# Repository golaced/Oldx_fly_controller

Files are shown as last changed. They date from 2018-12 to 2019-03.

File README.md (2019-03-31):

# 1 OLDX-开源多旋翼开发平台项目  
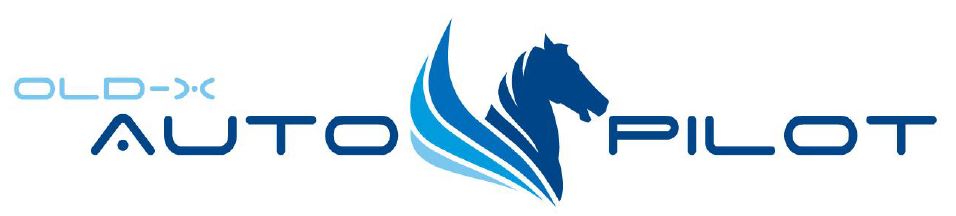
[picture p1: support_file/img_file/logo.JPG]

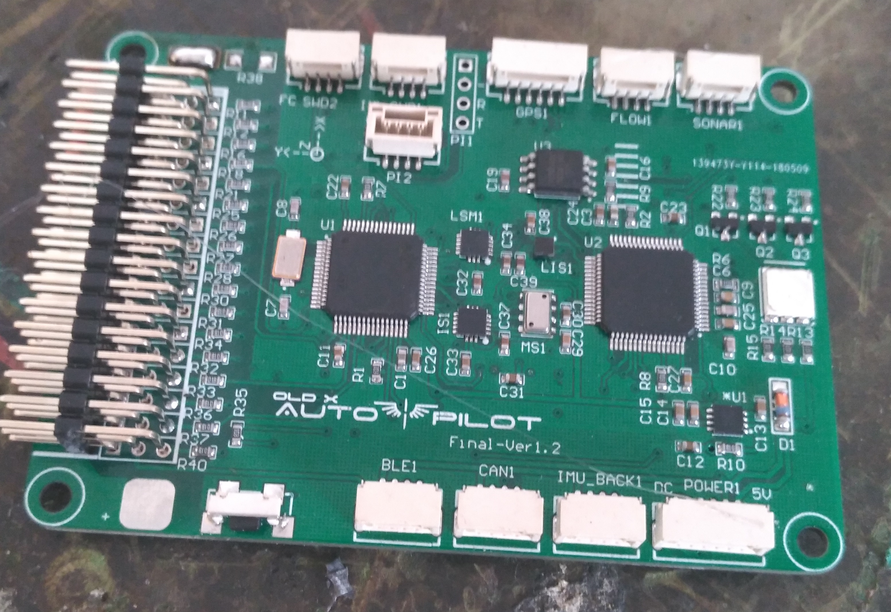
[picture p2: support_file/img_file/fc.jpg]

____OLDX多旋翼开发平台（OLDX-FC）是由北京理工大学自动化学院所属《北理云逸科技》团队开发的一个目前国内最完整的免费开源飞控项目，随着国内开源飞控的逐步发展如匿名、
INF、无名和ACFly飞控的陆续推出，如光流、气压计和GPS等相关算法已经逐步完善，但是相比Pixhawk等国外开源飞控平台的发展和定位仍然有发展空间。OLDX-FC于14年开始对多旋翼飞行器进行研究期间也经历过开源和借鉴的过程，为希望进一步推动国内开源飞控协作开发和
相互学习、相互分享的趋势，团队将该OLDX-FC转化为开源项目，采用自由捐赠的形式继续发展。<br>
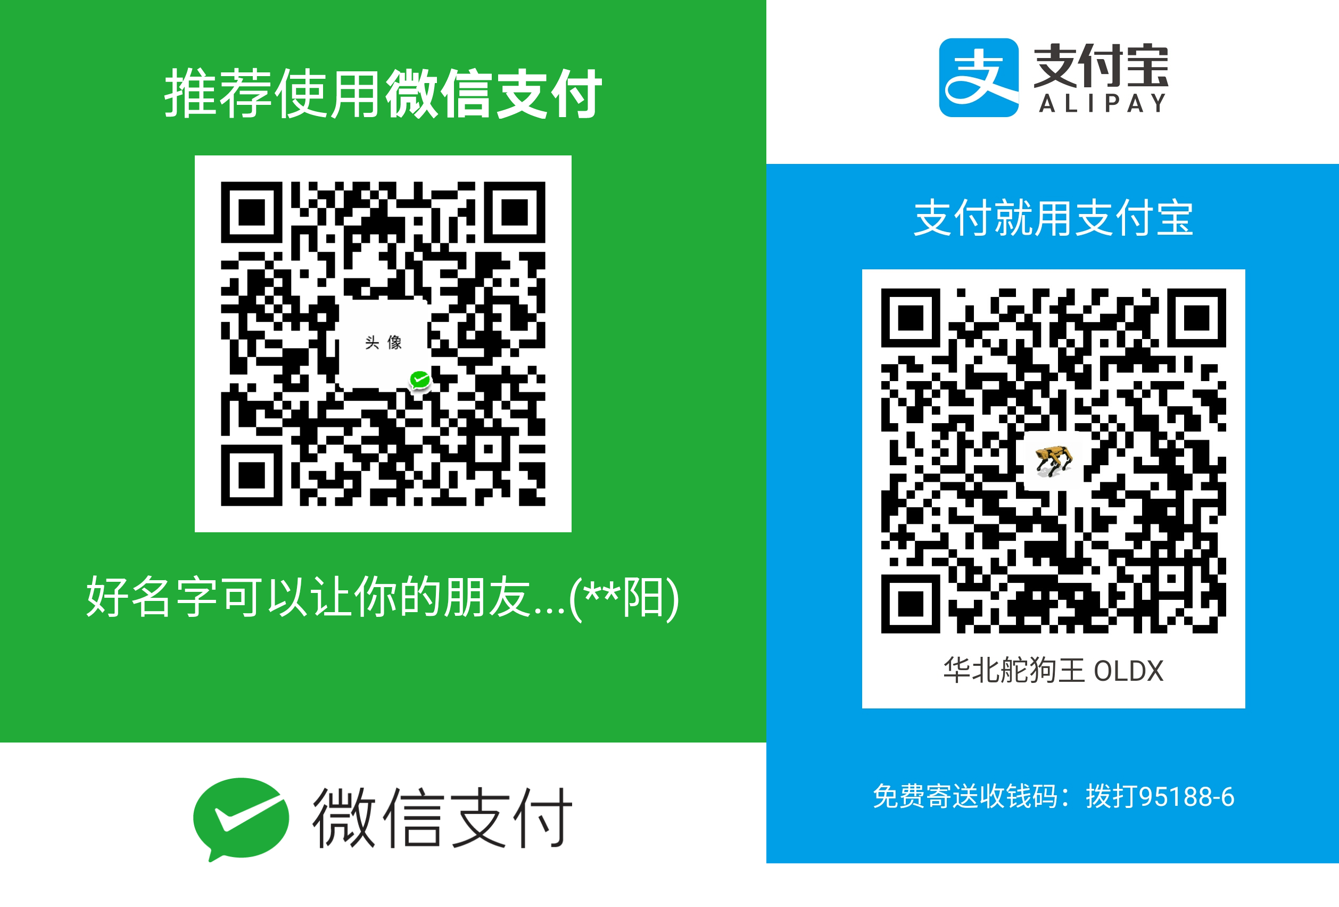
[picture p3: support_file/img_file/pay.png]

项目遵循GPL协议，能自由下载项目PCB进行加工使用但请勿作为商业用途，开源所有飞行控制和组合导航源码，可以进行修改和二次开发。<br><br><br>

**项目荣誉**

项目|奖项|年份
-------------|-------------|-------------
IMAV国际微小型无人机大赛|室外赛第3名  室内最佳自动化|2018
中航工业杯|三等奖|2018
IMAV国际微小型无人机大赛|室外赛第5名|2017
中航工业杯|二等奖|2017
中航工业杯|三等奖|2016

**-如果该项目对您有帮助请 Star 我们的项目-**<br>
**-如果您愿意分享对该项目的优化和改进请联系golaced@163.com或加入我们的QQ群567423074，加速开源项目的进度-**<br>

# 2 基本功能介绍
____OLDX-FC是一个基于STM32F4系列单片机的多旋翼飞控平台，其采用双处理器、双IMU冗余的设计，飞行控制和组合导航分别运行与不同的单片机中基于串口DMA进行高速数据交互
板载两套6轴惯性传感器、1个三轴磁力计、1个气压计并支持外部罗盘接入。组合导航CPU采用UCosII嵌入式操作系统基于卡尔曼滤波算法实现对GPS、光流、UWB和气压计数据的可靠
融合，从而实现室内外可靠的悬停和航线飞行，姿态和高度控制采用自抗扰（ADRC）控制算法实现对外部扰动的可靠控制同时具有响应快、信号跟踪性能好的特点，通过对自抗扰算法
改进实现了基于飞行器轴距、姿态、航向和高度三通道感度和快速调参。飞控在内部封装SDK二次开发接口和部分Demo，能快速实现一键起飞降落，视觉降落，目标跟踪和自主避障，
另外预留多个扩接口能作为地面机器人、无人车和无人船的硬件载体。飞控源码移植了Mavlink航向设置源码能实现基于Qground和MissonPlanner的任意航点、高度和速度的设置，
基于匿名地面站能实现对飞控内部任意融合结果、传感器参数、控制反馈期望和状态信息的实时显示和参数调节，基于板载NRF2.4通讯芯片能与地面手持遥控实现最远900米
的数据交互，实时显示飞行器经纬度、姿态，并对任意参数进行在线设定和修改，免去室外参数调节需要携带电脑和平板的不便。<br>



**飞控特性**：<br>
	*UCosII操作系统(正点原子)<br>
	*自抗扰姿态控制<br>
	*卡尔曼组合导航<br>
	*SDK快速开发<br>
	*Mavlink航线规划和匿名地面站快速调参<br>
	*移动遥控端状态显示和参数在线修改<br>
	*GPS导航、视觉导航、自动降落、光流图像定位<br>

**飞控性能演示视频连接：**<br>
	[SDK开发演示](https://v.youku.com/v_show/id_XMzc4MzAyMDU4MA==.html?spm=a2hzp.8244740.0.0&f=49551028) <br>
	[室外GPS航线测绘和地面站航点设置](https://i.youku.com/i/UMTU1NTgzMzYw?spm=a2hzp.8253869.0.0) <br>
	[视觉固定目标降落](https://v.youku.com/v_show/id_XMzk2OTMyNzE4MA==.html?spm=a2hzp.8253869.0.0) <br>
	[视觉移动小车降落](https://v.youku.com/v_show/id_XMzc0MTI4NzQ2NA==.html?spm=a2hzp.8253869.0.0) <br>
	[室内二维码地标阵列定位](https://v.youku.com/v_show/id_XMjc2MDAxMDI1Mg==.html?spm=a2hzp.8253869.0.0) <br>
	[室外光流悬停](https://v.youku.com/v_show/id_XMjc1NzI1NDQ4NA==.html?spm=a2hzp.8253869.0.0) <br>
	[室内气压计定高](https://v.youku.com/v_show/id_XMjcyNjM2MzU5Mg==.html?spm=a2hzp.8253869.0.0) <br>

# 3 PCB硬件参数
____OLDX-FC硬件采用4层板设计，通过外部电源模块进行供电支持2S~4S电池供电，具有最大12路PWM输出4路AD信号输入，板载NRF2.4通讯芯片，预留6路串口1路CAN接口<br>
  
**硬件参数：**

项目|参数
-------------|-------------
处理器|STM32F405RGT6-2
处理器性能|32Bit ARM Cortex-M4 168MH
陀螺仪 加速度计|ICM20602 + LSM6DS33
磁力计|LIS3MDL
气压计|MS5611
预留接口|GPS-1 串口-4 CAN-1 图像-1
PWM 输出通道|8 通道PWM + 4 路AUX
供电|5V输入 IO输出5V
飞行器类型|四旋翼 六旋翼 八旋翼 共轴六旋翼
高度悬停精度|±0.02m（超声波） ±0.1m（气压计）
位置悬停精度|±0.2m（GPS） ±0.1m（光流）

<br><br>
**飞控外壳：**<br>
____提供飞控3D打印外壳STL文件，设计为气压计增加缓冲空间并设计了减震球底座。
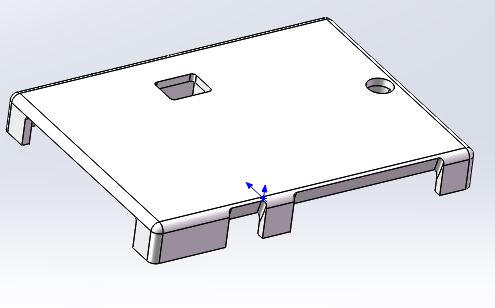
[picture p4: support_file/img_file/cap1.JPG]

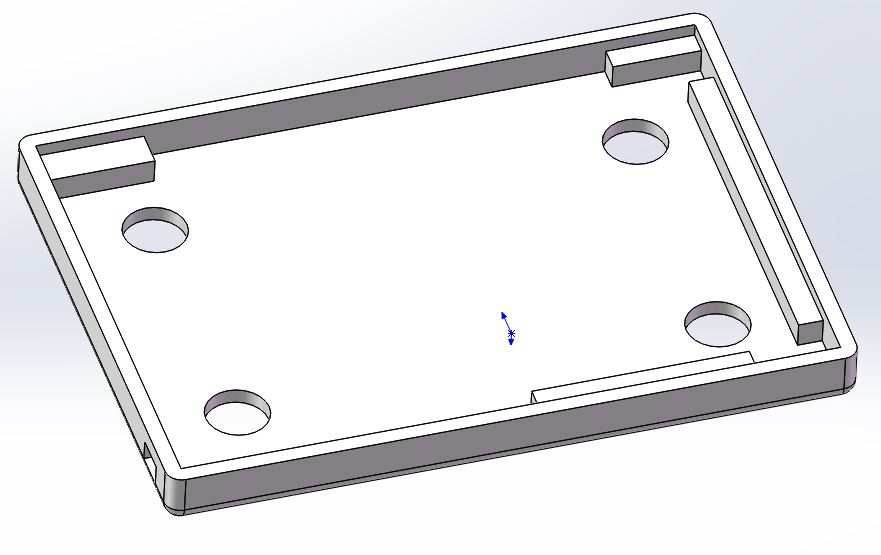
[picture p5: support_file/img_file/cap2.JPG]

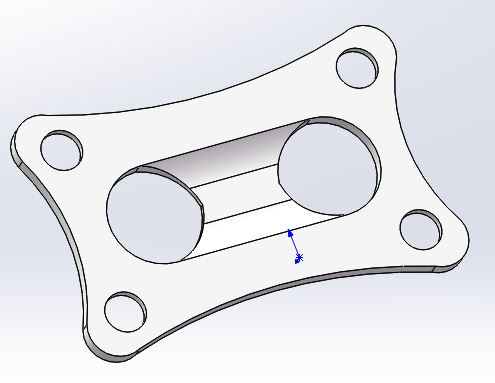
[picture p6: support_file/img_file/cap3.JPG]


# 4 软件说明
____OLDX-FC基于C语言和Keil5进行开发，飞行控制部分基于匿名早期裸奔程序架构，采用状态机调度保证不同线程的运行周期，
对其姿态控制部分进行修改，采用SO3下的旋转矩阵求取外环控制误差，姿态内环采用改进ADRC控制器保证对给的角速度的
稳定跟踪；高度控制部分替换原始互补滤波融合算法采用扩展卡尔曼滤波器融合气压计和加速度计，同样使用ADRC控制器控制
高速速度环。位置方面通过串口数据接收组合导航模块解算机体速度和位置，采用位置+速度+加速度三环控制飞行器位置；
通讯方面在保留匿名上位机调参功能外增加2.4G无线通讯，可脱离遥控器采用体感进行飞行器控制，另外移植Mavlink通讯协议实现
与Qground和MissonPlanner地面站的通信，实现室外飞行器航点设置和轨迹显示；增加SDK二次开发接口，封装了多种常用函数，如
速度给定，位置移动给定，航向飞行，图像目标对准，图像目标跟踪，地标引导降落的多个子API，通过简单的流程书写既可以实现
复杂的智能导航、图像导航功能，十分适合于Demo研发、电子竞赛、无人机竞赛和DIY开发中。<br>
____组合导航模块基于UCOSII操作系统，基于UKF和KF算法完成GPS、UWB、光流与加速度传感器数据的融合，采用非线性AHRS算法实现
可靠的姿态解算和机体加速度解算，同时预留CAN总线接口方便后续外扩其他传感器数据。

<br><br>
**飞行控制模块**

项目|参数
-------------|-------------
姿态解算|互补滤波(匿名)
高度融合|扩展卡尔曼(PX4)/抗差卡尔曼
姿态控制|SO(3)误差(PX4)+PD(角度)+ADRC(角速度)
高度控制|PD(高度)+ADRC(垂直速度)
位置控制|PD(高度)+PID(机体速度)+P(机体加速度)
通讯接口|2.4G无线通讯(匿名+OLDX手持遥控器) 串口数传(匿名+Mavlink)
控制方式|遥控器(PPM+SBUS) OLDX手持遥控器 SDK自主飞行
外部控制信号|4路舵机输出  支持使用飞控姿态控制两轴舵机云台稳相和无刷云台目标跟踪(RobotMaster)
地面站支持|匿名地面站(参数显示+波形显示+参数设置)  Qground/MissionPlanner(位姿轨迹显示+航点写入)

<br><br>
**组合导航模块**

项目|参数
-------------|-------------
姿态解算|非线性AHRS/梯度下降/扩展卡尔曼/互补滤波(匿名)
位置融合|抗差卡尔曼/无迹卡尔曼(AutoQuad)
传感器接口|GPS(NEO-8M 乐迪迷你)+UWB(INF)+光流(Pixflow/OLDX-AMF)+超声波(串口/PWM)+激光测距仪(VL53L0X)

# 5 飞控使用教程
## 5.1 PCB接口说明

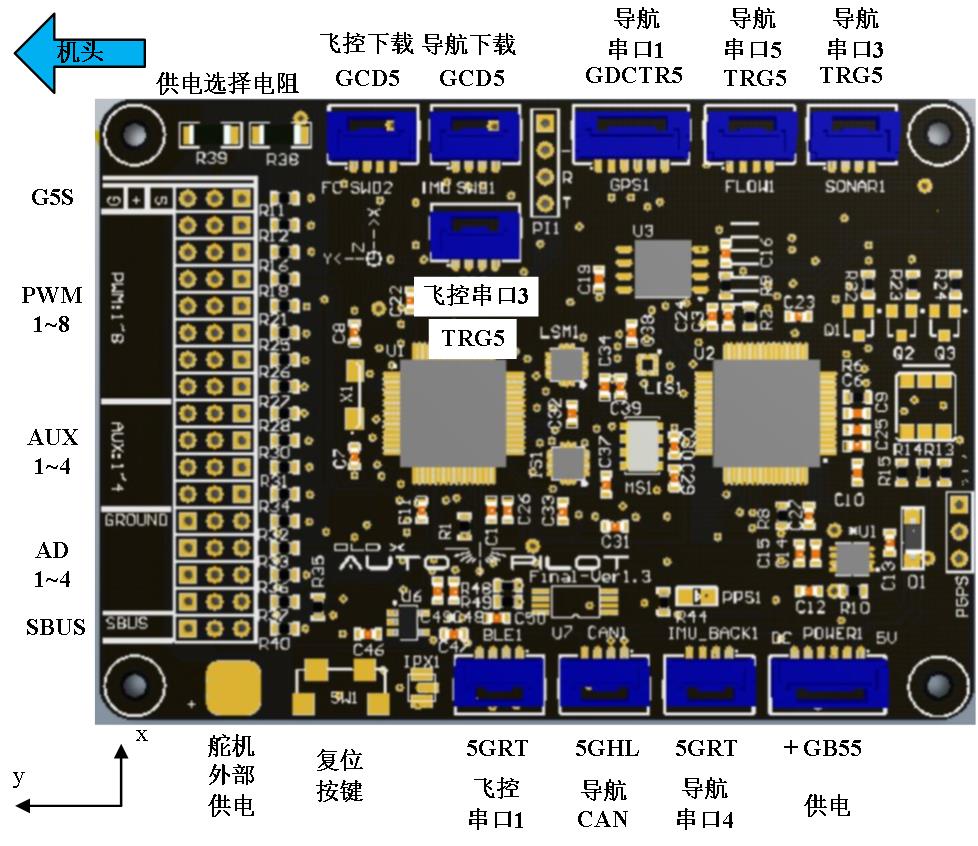
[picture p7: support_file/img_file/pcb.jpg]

<br><br>

接口|说明|支持模块
-------------|-------------|-------------
飞控下载|飞控模块SWD下载口|download_fc模块 C->SCLK D->SWD
导航下载|导航模块SWD下载口|download_stlink模块
导航串口1|GPS和外部罗盘IIC接口|乐迪M8N Mini GPS C->SCL D->SDA
导航串口5|光流传感器接口|Pixflow  OLDX-AMF
导航串口3|超声波接口|US100 (串口模式下T->T R->R)  北醒激光测距模块
导航串口4|预留传感器接口|
导航CAN|预留CAN总线接口|
飞控串口3|图像处理接口|树莓派  Odroid-XU4 （图像处理器需自行供电）
飞控串口1|数传接口|匿名数传 3DR数传  CUAV WIFI数传
PWM1~8|电调接口|400Hz
AUX1~4|电调9~12/舵机控制接口 1俯仰 2横滚 3投递器开关|两轴舵机云台 两轴无刷云台
AD1~4|模拟电压采集接口|压力传感器AD(0~3.3V)
SBUS|接收机接口|天地飞接收机 Futaba接收机
舵机供电选择|R39外部供电 R38飞控供电 （任选一）|
供电|采用6P自锁双头端子线与供电模块连续|power模块 +->DC B->蜂鸣器信号 5->5V降压输入

<br><br>
**OLDX飞控最少所需配置**

模块组合|实现功能
-------------|-------------
飞控+Power模块|手动飞行/气压定高
飞控+Power模块+光流|手动飞行/气压定高/超声定高/光流悬停/SDK飞行
飞控+Power模块+GPS|手动飞行/气压定高/GPS航线飞行/SDK飞行
飞控+Power模块+GPS/光流+树莓派/Odroid|手动飞行/气压定高/GPS航线飞行/SDK飞行/图像导航/视觉降落

<br><br>
**接线示意图**
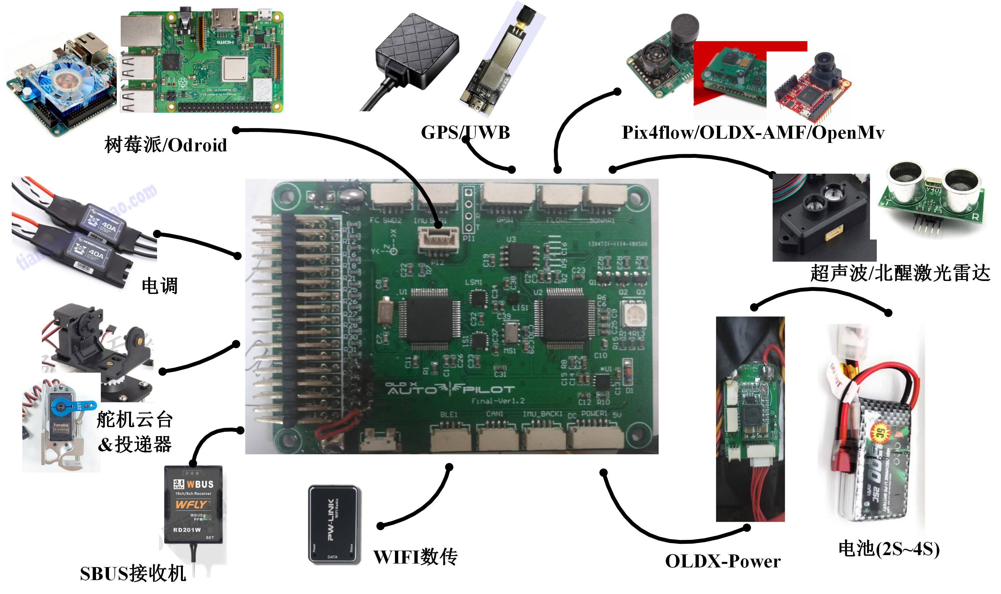
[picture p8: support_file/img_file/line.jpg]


## 5.2 程序宏定义和飞控配置说明
### 5.2.1 遥控器通道

通道|功能|通道说明
-------------|-------------|-------------
CH1|横滚通道|
CH2|俯仰通道|
CH3|油门通道|
CH4|航向通道|
CH5|SDK模式使能|  通道值<1500(关闭自动SDK飞行) 通道值>1500(使能自动SDK飞行)
CH6|返航和自动起飞| 通道值<1500(打开AUX3口开关) 通道值>1500(关闭AUX3口开关)
CH7|位置模式|  通道值<1500(手动) 通道值=1500(速度悬停) 通道值>1500(位置悬停)
CH8|高度模式|  通道值<1500(超声波 气压计自动切换) 通道值=1500(气压计) 通道值>1500(手动)

**飞行器解锁上锁**：外八遥控操作<br>
**飞行中关闭遥控器**：自动返航/自动降落/电机急停<br>
**自动起飞和智能飞行**：CH5>1500 CH6>1500 CH7>1500 CH8<1500  状态下外八解锁  并把油门置于中位(自主飞行中任意遥感不在中位均会进入自主飞行模式，
回复中位后继续执行当前任务。需要取消飞行则保证CH5<1500) <br>
**自主任务状态机重置**：在飞行器执行自主任务后无论自动降落或者人工打断都需在着陆上锁后保证CH5<1500 CH7<1500<br>
**飞行中自动返航**：无论在自主飞行或人工遥控飞行中 如果CH6通道值从大于1500切换到小于1500则进入失控策略，过程中可以通过人为遥控打断，并重新进行触发<br>
**陀螺仪校准**：CH8<1500 时CH7从小于1500到大于1500 快速切换多次<br>
**磁力计校准**：CH8>1500 时CH7从小于1500到大于1500 快速切换多次，进入模式后BB响持续发声，蓝色1s间隔闪烁<br>

## 5.3 飞行器配置和控制参数调整说明
### 5.3.1 飞行器配置
（1）飞控模块include.h<br>

宏定义|说明
-------------|-------------
USE_OLDX_REMOTE|使用OLDX手持遥控器代替传统遥控器
AUTO_MISSION|使能SDK飞行 
MAXMOTORS|最大电机数量（4/6/8/12）
FLASH_USE_STM32|使用STM32内部EPRoom模拟Flash  使能则无法存储GPS航点
YAW_INVER|航向控制输出方向 用于电机转向与标准方向不对下的软件调整，不用重新安装电机
YAW_FC|不使用磁力计修正航向
MAX_CTRL_ANGLE|最大控制姿态角度
MAX_CTRL_YAW_SPEED_RC|最大控制航向角速度
ESO_AI|姿态控制内环ADRC b0参数（0表示不使用ADRC控制器）
ESO_YI|航向控制内环ADRC b0参数（0表示不使用ADRC控制器）
HOLD_THR_PWM|预设悬停油门
DEBUG_MODE|室内则封闭PWM输出，解锁后电机不转动可以作为室内Debug使用
TUNING_ONE_AXIX|使能则参数调节时仅针对一个轴
TUNING_X/ TUNING_Z|单轴调参目标
USE_KF|使用带估计加速度偏差的卡尔曼滤波器估计高度否则使用PX4提供的EKF高度估计算法
USE_CARGO|使用AUX3的舵机投递器

（2）飞控模块oldx_api.h<br>

宏定义|说明
-------------|-------------
LAND_SPD|自动降落速度
MAX_WAYP_Z|最大航点高度限制
WAY_POINT_DEAD1|航点达到判断死区
LAND_CHECK_G|着地检测重量加速度
LAND_CHECK_TIME|着地检测条件判断时间
YAW_LIMIT_RATE|旋转航向最大角速度限制 

（3）导航模块include.h<br>

宏定义|说明
-------------|-------------
USE_UKF_FROM_AUTOQUAD|使用Autoquad提供的UKF融合算法(存在Bug)
UKF_IN_ONE_THREAD|UKF融合时不使用UcosII系统
USE_US100/ USE_KS103/ USE_LIDAR|定高传感器数据选择
SONAR_SAMPLE1/ SONAR_SAMPLE2/ SONAR_SAMPLE3|高度传感器数据采样频率
USE_IMU_BACK_IO_AS_SONAR|使用串口4采集高度传感器数据
SONAR_USE_FLOW|直接使用Pixflow传感器自带超声波高度数据

<br><br>
**飞行器型号设置**：<br>
（1）采用如下宏定义定义你的飞行器<br>

```
#if defined(M_DRONE)
#define M_DRONE_ID     //单片机id_chip值
#define PX4_SDK 0  
//#define PX4_LINK
#define USE_MINI_FC_FLOW_BOARD 0 
#define USE_VER_8_PWM 1  
#define USE_VER_8 0  
#define USE_VER_7 1
#define USE_OLDX_REMOTE 0

#define BLDC_PAN
#define W2C_MARK
#define USE_CIRCLE 0
//#define USE_LED 
//#define USE_CARGO     //可修改
#define AUTO_MISSION    //可修改

//#define USE_KF	    //可修改 
#define USE_UWB
#define MAXMOTORS 		(4)		//可修改
#define FLASH_USE_STM32 0       //可修改
#define YAW_INVER 	  0		    //可修改
#define YAW_FC 0  				//可修改
#define MAX_CTRL_ANGLE			30.0f	//可修改
#define MAX_CTRL_YAW_SPEED_RC   200	    //可修改

#define ESO_AI 22  //可修改
#define ESO_YI 22  //可修改
//
#define TRAJ1_1  2//2 circle 1 line  3 way points   4 jerk  5 car
#define HOLD_THR_PWM  LIMIT(500,0,500)  //可修改
#endif
```
<br>
并在24~42行"唯一"定义该机型：
<br>

```
#define M_DRONE
//#define M_DRONE250X4
//#define M_DRONE_330X6
//#define M_DRONE_330 
//#define M_DRONE_PX4
//#define M_CAR
```

<br>
并在init.c 43行定义飞控对应2.4G通讯通道CHE，修改188行 mode_oldx.rc_loss_return_home选择失控模式(0上锁 1返航 2降落 3无视)
<br>

```
switch(id_chip)
{
case M_DRONE_ID: CHE=25;break;
case IMAV2: CHE=22;break;
case IMAV3: CHE=33;break;
default: CHE=11;break;
}
```

<br>
并在pos_ctrl.c 854行定义使用的SDK：
<br>

```
switch(mission_sel_lock)
{
case 0:
switch(id_chip)
{
case M_DRONE_ID: mission_flag=mission_test_gps(T); break;//你的SDK
case IMAV2: mission_flag=mission_search(T); break;
case IMAV3: mission_flag=mission_test_gps(T); break;
default:mission_flag=mission_test_gps(T); break;
}	
break;
```

<br>
并在scheduer.c 152行定义UART_UP_LOAD_SEL选择上位机波形显示队列
<br>

### 5.3.2 参数调节
____飞控已经集成基础参数调节功能在完成飞行器机型设置和固件更新后，进行传感器校准即刻起飞或者进行参数调节。<br>
(1)远程调参与波形显示<br>
____飞控默认采用2.4G无线与OLDX手持遥控端进行通讯，参数调节可以直接通过遥控器实现，另外手持遥控器同时具有USB虚拟串口，
遥控器工作后连接PC机则可以使用匿名地面站进行参数调节(115200默认波特率)和参数波形显示。(注：对手持控制器来说需要在PID参数界面
等等数据全部接受完成后在进行调参，否则会出现参数误写入引起的炸鸡；对地面站同样也是建议在数据通信正常后最少读取5次PID参数避免误写入问题)
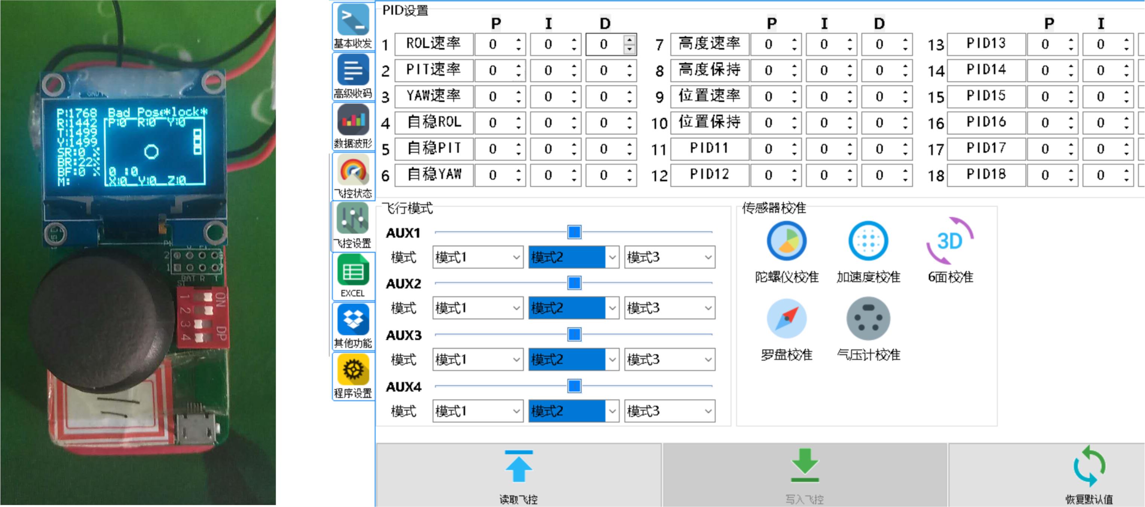
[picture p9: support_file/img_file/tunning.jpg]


(2)姿态参数调节<br>
____飞控安装好后首先需要进行姿态参数的调节推荐采用万向轴或烤四轴的方式固定飞行器进行参数调节，通过选择调参模式确认是单轴还是全向调参：

```
TUNING_ONE_AXIX 0
TUNING_X 0
TUNING_Z 0
```

默认都为0则飞行器全向参数都可调节，则以该情况为例设置 UART_UP_LOAD_SEL=11 使能上位机波形显示为姿态参数调节序列，通过CH6(>1500外环)能选择显示内环还是
外环的期望和给的参数，则波形中Ax Ay Az为期望的横滚 俯仰 航向值，Gx Gy Gz为对应反馈值，Hx Hy Hz为对应误差。参数调节时如果外环PID参数有值则
遥杆给定期望角度，如无值则给定期望角速度。<br>

A.如飞行器机架小于550轴距可直接调整感度来快速完成参数调节，使用手动模式起飞保证飞行器离地观测姿态控制是否响应迅速，
是否存在超调和抖动，感度对应PID参数为：<br>

参数|说明|默认值
-------------|-------------|-------------
PID17-P|横滚、俯仰感度(增大则等于增大飞机调节增益)|1000
PID17-I|航向感度|1000
PID17-D|高度感度|1000

<br><br>

飞行器机型|主要动力配置|飞行器感度
-------------|-------------|-------------
330X4四轴|3s 4000mah  1500kv*4 好赢乐天15A 8寸桨|俯仰:1000    航向:1000   高度:1000   b0:22
450X4四轴|4s 4000mah  920kv*4 好赢乐天20A 9寸桨|俯仰:820    航向:1000   高度:1100   b0:22
6轴泡沫机|3s 10000mah  920kv*6  Emax 40A  8寸桨|俯仰:300    航向:200   高度:100  b0:3.5
共轴反桨6轴涵道|6s 10000mah 450kv*12 Emax40A 9寸桨|俯仰:250   航向:280   高度:68   b0:2.2
6轴飞行器+小车底盘|6s 16000mah *2 180kv *6 Emax40A 14寸桨|俯仰:325 航向:168 高度:100 b0:0 II:400 ID:4500 OP:368 P_GAIN:100

B.如飞行器轴距较大，电机KV值较小则不推荐采用起飞调参的方式，在调试架上固定好飞行器后采用手动模式解锁调参并内外环波形曲线。
调参时首先将ADRC控制器b0置0不使用其控制输出，将外环PID清0仅调整角速度环，解锁后观察飞行器是否能较好地跟踪遥控给定速度，
在能保证基本跟踪上后将姿态ADRC b0在22-300进行调整(默认220)，如果飞机出现晃动则减小，出现顿挫则增大，在基本实现跟踪期望速度后(可存在一定
滞后，特别是大飞机)通过拉拽飞行器轴造成外部扰动和控制器饱和来确定是否需要增大D，如果出现按压时的超调可增大D来保证回弹的柔和。<br>
在完成内环参数调节后，设置外环P参数(默500-700)，在保证出现一定超调下的P时增加D达到最终回中无快速无超调(550以下小飞机可能不需要D)，之后
同样采用人为拉拽或按压测试控制器饱和回中是否出现超调和震荡判断参数是否合适。<br>
对航向来说一般仅需要调整感度既可以满足一般应用，如有更高性能要求可采用类似如上的方式进行参数调节，另外航向ADRC b0参数推荐仅在小轴距飞行器
上使用，则姿态调节对应PID参数表如下：<br>

参数|说明|默认值
-------------|-------------|-------------
PID1-P|横滚、俯仰 内环P|700
PID1-I|横滚、俯仰 内环I|200
PID1-D|横滚、俯仰 内环D|2200
PID2-P|姿态ADRC  b0|220
PID2-I|航向ADRC  b0|220
PID2-D|ADRC 控制死区|268
PID3-P|航向 内环P|1200
PID3-I|航向 内环I|100
PID3-D|航向 内环D|1200
PID4-P|横滚、俯仰 外环P|700
PID4-I|横滚、俯仰 外环I|0
PID4-D|横滚、俯仰 外环D|0
PID6-P|航向 外环P|800
PID6-I|航向 外环I|50
PID6-D|航向 外环D|300

在完成参数调节后可以采用两种方式将其保存在Flash中，对于感度可以采用遥控触发陀螺仪的方式写入(水平静置)，但还是推荐采用在代码里修改的方式。
其中对于ADRC b0参数在机型宏定义中修改，飞行器感度在Debug watch中修改后选择校准陀螺仪(见6.4.2小节)保存，姿态PID则在parameter.c 40行中进行修改:

```
float pid_att_out[3]={0.7,0.0,0.0};
float pid_att_in[3]={0.7,0.2,2.2};

float pid_att_out_yaw[3]={0.8,0.05,0.3};
float pid_att_in_yaw[3]={1.2,0.1,1.2};
```

(3)高度参数调节<br>
____高度参数调节方式类似姿态调节，如对性能要求不高则可采用默认参数通过调整感度的方式实现快速起飞。另外也可以采用上位机
对比期望波形的方式调节，将UART_UP_LOAD_SEL=2显示高度控制波形序列，之后同样采用将ADRC b0置0先内环后外环的方式，调节时
注意保证姿态参数已经可靠，出现震荡时快速切换到手动模式降落。

```
scheduler.c 282行
case 2://高度控制，速度z控制和速度xy
data_per_uart1(
ALT_POS_BMP_UKF_OLDX*1000,ultra_ctrl.exp,baro.h_flt*100,
ALT_VEL_BMP_UKF_OLDX*1000, wz_speed_pid_v.exp,wz_speed_pid_v.now,
VEL_UKF_Y*100,VEL_UKF_X*100,0,
(int16_t)(Yaw_fc*10),(int16_t)(Pit_fc*10.0),(int16_t)(Rol_fc*10.0),thr_value,0,0/10,0);break;	
```											

参数|说明|默认值
-------------|-------------|-------------
PID7-P|高度 内环P|500
PID7-I|高度 内环I|300
PID7-D|高度 内环D|1680
PID8-P|高度 外环P|1000
PID8-I|高度 外环I|100
PID8-D|高度 外环D|0
PID12-P|高度 ADRC b0|15
PID12-I||
PID12-D|高度 ADRC 死区|10

保存参数类似姿态控制的方式，参数在程序如下部分：

```
height_ctrl.c 41行

ultra_pid.kp = 1.0;
ultra_pid.ki = 0.1;
ultra_pid.kd = 0.0;

wz_speed_pid.kp = 0.5;
wz_speed_pid.ki = 0.3;
wz_speed_pid.kd = 1.68;
wz_speed_pid.fp=0.2;

//adrc
eso_pos_spd[Zr].b0=15;
eso_pos_spd[Zr].eso_dead=0.01*1000;	
eso_pos_spd[Zr].eso_for_z=1;

```			

(4)位置参数调节<br>
____位置参数调节方式可采用上述调参方式其波形序列为UART_UP_LOAD_SEL=3(速度)，UART_UP_LOAD_SEL=5(位置)。
调节时注意保证姿态参数已经可靠，出现震荡时快速切换到手动模式降落。如定高参数以稳定可采用气压计定高起飞，
在达到齐胸高度后先切换速度模式，给定姿态观测回中后是否有可靠制动是否存在刹车时晃动，如角度太大则减小速度内环P即可(其他参数可不调节),
在速度环制动平缓柔和且悬停无明显晃动后，切入位置模式观测是否还存在漂移，通过给的速度制动观察飞行器控制效果，对小飞机仍然
可采用人为拉拽的方式验证。

参数|说明|默认值
-------------|-------------|-------------
PID9-P|位置 内环P|330 (对大轴距飞行器可降低到180)
PID9-I|位置 内环I|0
PID9-D|位置 内环D|0
PID10-P|位置 外环P|360
PID10-I|位置 外环I|50
PID10-D|位置 外环D|0

保存参数类似姿态控制的方式，参数在程序如下部分：

```
pos_ctrl.c 321行

nav_pos_pid.kp=0.36;
nav_pos_pid.ki=0.0500;
nav_pos_pid.kd=0.0;
nav_pos_pid.dead=0.01;

nav_spd_pid.f_kp=0.2;
nav_spd_pid.kp=0.33;
nav_spd_pid.ki=0;
nav_spd_pid.kd=0;
nav_spd_pid.max_exp=0;

nav_spd_pid.flt_nav=1;//修改为0.356左右可平滑制动手感  目前已经在程序中增加S函数保证制动平滑
```			

## 5.4 手持遥控器(OLDX-Remote)介绍
____为提高调参速度减少户外飞行所需PC机和上位机设备,OLDX飞控设计了一个手持端遥控器，其除了能使用体感模式遥控飞行器外，还能代替PC地面站进行实时参数调节，
另外其实时回传SDK主状态机和子状态机运行状态，期望高度速度信息和航线航点信息，能实时了解当前SDK运行状况和下一时刻飞行器的目标任务，解决了飞行器自主
飞行中对其内部状态难以获取的问题。
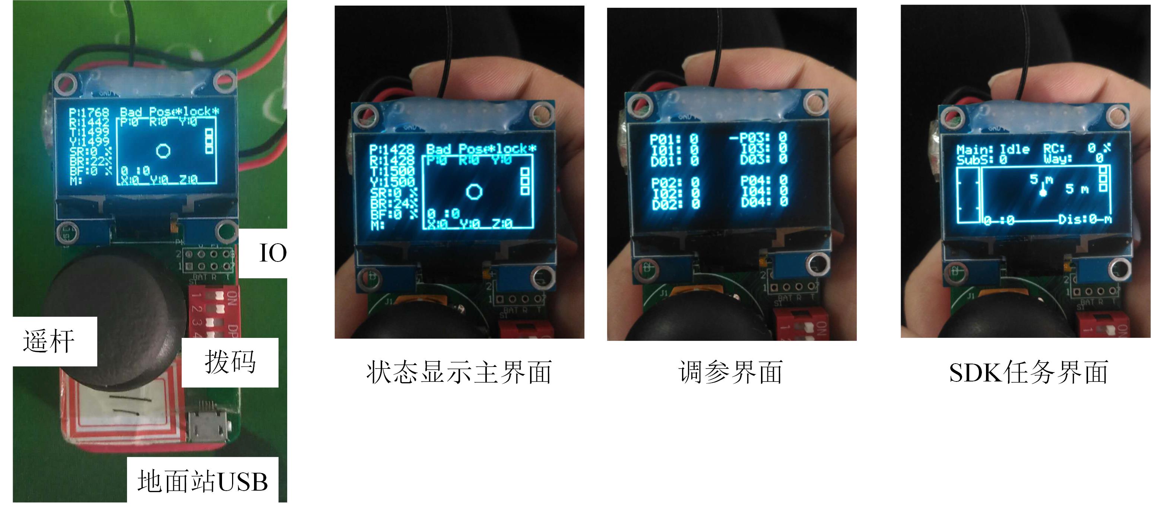
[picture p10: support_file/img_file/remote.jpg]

### 5.4.1 界面介绍
____OLDX-Remote开机后会显示当前遥控器通道请保证其与飞控中一致（之前在线修改），遥控器目前具有三类界面，（1）主界面：显示飞行器高度，姿态，电压和飞行时间等常用数据（2）PID参数界面与PC端地面站对应显示飞行器内部参数（3）
SDK界面：显示航线和自主任务命令，状态机状态。则各界面下英文缩写如下：

主界面|说明
-------------|-------------
P|OLDX-Remote 俯仰遥杆值(体感)
R|OLDX-Remote 横滚遥杆值(体感)
T|OLDX-Remote 油门杆值(遥杆)
Y|OLDX-Remote 航向杆值(遥杆)
SR|飞控与OLDX-Remote间的通信强度
BR|OLDX-Remote电量
BF|飞行器电量(飞行中小于25%则需尽快降落)
M|飞行器模式 Mual->手动  ALT B->气压计 ALT S->超声波 Pos->位置参数调节
Bad Pos|定位模式状态  Bad Pos->无定位 GPS->卫星数量(推荐8颗以上起飞) Opt->光流质量(推荐120以上地面起飞)
lock|飞行器锁定情况
矩形界面中P|飞行器俯仰角
矩形界面中R|飞行器横滚角
矩形界面中Y|飞行器航向角
矩形界面中 0:0|解锁后飞行时间
矩形界面中X,Y,Z|飞行器局部X轴位置(米)
矩形界面中 三个正方形点| 从上到下 *GPS连接  *图像设备连接 *光流模块连接
中心圆圈和实心点|单成像中c2c结构体pix_x,y有数会显示原点，可使用其来判断图像目标十分识别和在图像中的像素位置

<br><br>

PID参数界面|说明
-------------|-------------
PIDX-X|上位机中对应参数
左右拨动遥感到底2s左右可切换界面|
左右上下选择PID参数|
点击遥控出现*则选中该参数|选中下左右增加100参数 上下增加10参数
选择下再次点击退出选中—|遥控器每5s读取飞控数据 选中下不读取 
选中中长按遥感遥控发出BB声则参数写入|对CHE遥控通道来说其写入 需到主界面进行相同操作 同时会校准遥控IMU

<br><br>

SDK界面|说明
-------------|-------------
main|Idle(状态机默认状态 该状态自动起飞后才会运行SDK)  Mission(SDK模式)  Safe(状态机保护进入普通悬停模式  需降落上锁后复位所用遥控开关方可清除)
RC右方%|飞行器电量
Subs|子状态机状态
Way|剩余航点数量
左方竖条|高度期望和反馈  位置模式(期望为横线当前为矩形中心) 速度模式(显示上升下降期望速度)
矩形框|位置期望和反馈   中心为当前飞行器位置，原点为期望位置(坐标系为x-y  东-北)，坐标系尺度自动缩放，小横线表示飞行器机体方向
Dis|下一个航点距离(米)

### 5.4.2 遥控器模式介绍
OLDX-Remote板载MPU6050 IMU传感器可实现体感操作，在include.h中修改如下：

```
#define USE_RECIVER_MINE 1
```

体感操作遥控器遥感上下对应油门，左右对应航向，前后倾斜对应俯仰，侧斜对应横滚。飞行器解锁为遥感右下2秒。通过在主界面长按遥感按键
可以实际对遥控器中位的零偏校准。

# 6 首次飞行说明(四轴机型为例)
## 6.1 飞控安装和程序下载
____首先将OLDX飞控沿机头方向安装在机体中心，推荐使用减震处理，(不在中心可能由于旋转效应造成而外加速度影响制动或悬停)，下图给出了典型飞行器的电调PWM
信号线顺序和螺旋桨转向，如电机转向与图中相反可以重新安装或者定义YAW_INVER为1：

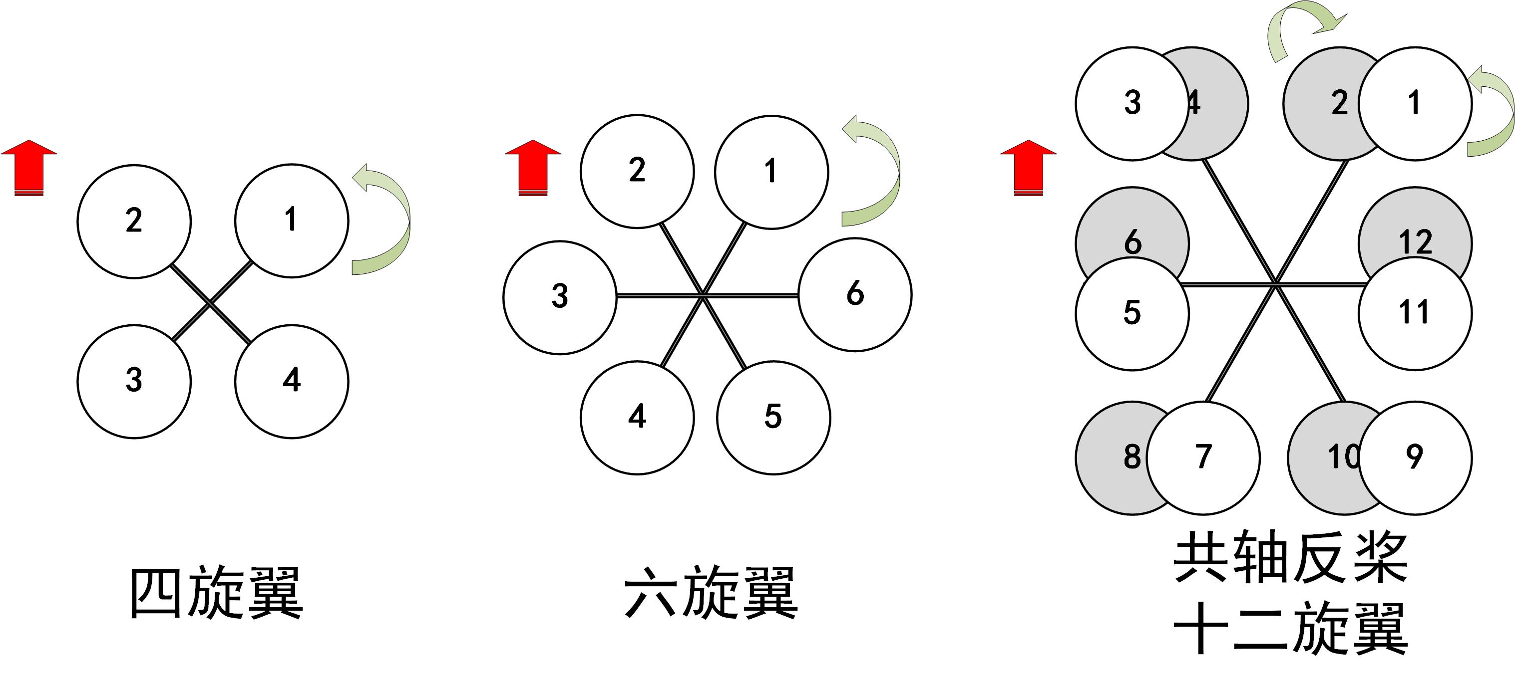
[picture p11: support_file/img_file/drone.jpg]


安装好电调和飞控后，将Power模块使用6P双头自锁线与飞控供电端连接，同时将Power端DC输入与飞行器整体供电输入焊接在一起(2S~4S),将螺旋桨解除，采用如下图的方式
使用download和ST-link下载器连接飞控供电：
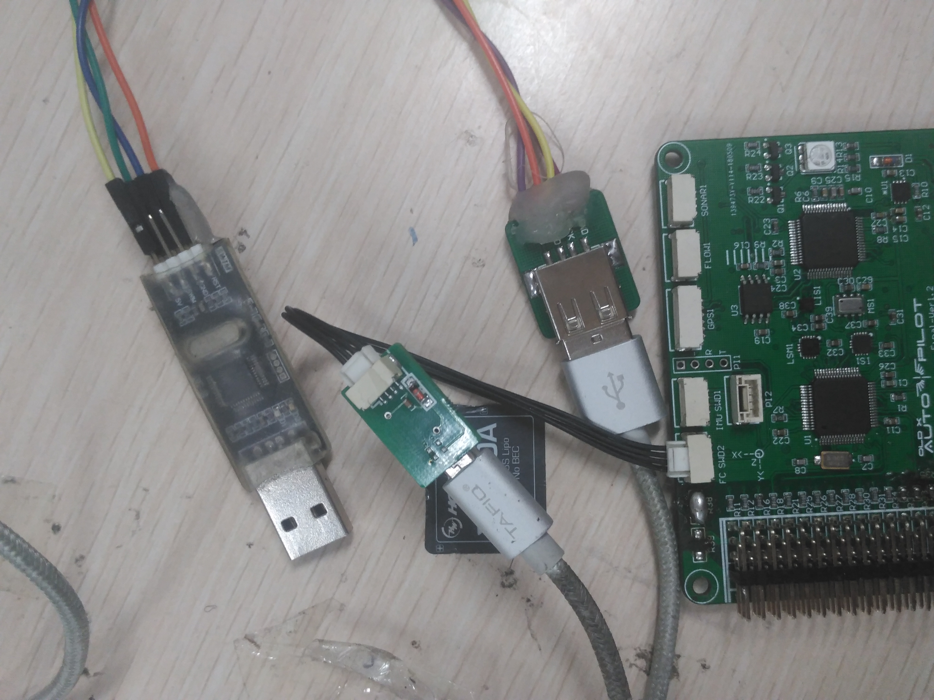
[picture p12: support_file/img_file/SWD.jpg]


____在确认ST-Link驱动安装无误后首先向FC飞控单片机下载程序，下载完成后可以采用Debug模式运行或者重新上电，如系统正常则蜂鸣器会响并且LED闪烁，之后采用同样方法
向IMU导航单片机下载程序，运行后查看Watch中lis3mdl结构体(如没有请手动右键添加，同时保证菜单View下拉中Periodic Update选择)中Acc_I16、Gyro_16、Mag_Adc是否是数
如有数(传感器正常)则将电路板水平静置将Acc_CALIBRATE和Gyro_CALIBRATE分别置1，查看Acc_Offset和Gyro_Offset保存的当前传感器零偏，复位芯片后查看读书是否基本一致
验证板载Flash芯片正常。<br>
____完成IMU下载和电路验证后重新Debug飞控单片机，此时开机蜂鸣器应当会发出开机音乐,同样mpu6050_fc结构体中传感器参数是否刷新，校准传感器复位芯片检测Flash中
是否读出上次标定参数，如全部正常则硬件部分基本无误可以尝试飞行。<br>

注：如将如下部分进行修改则开机可以模拟Pixhawk蜂鸣器声音

```		
//beep.c 145行
case START_BEEP:
music_sel=	START_BEEP;
Play_Music(start_music_windows,0,sizeof(start_music_windows)/2);	
break;
		
//修改为
case START_BEEP:
music_sel=	START_BEEP;
Play_Music(start_music_px4,0,sizeof(start_music_px4)/2);	
break;
			
```		

**另外飞控安装时最好使用黑色泡沫覆盖气压计部分并3D打印外壳，防止飞行中气压计受气流干扰！！**

## 6.2 飞控配置和起飞前传感器校准
____在完成飞控安装和电路验证后，安装之前所述方式定义自己的飞行器和SDK，调整参数或采用默认参数飞行，首次飞行器需再次进行传感器校准。<br>
（1）首先将飞行器水平放置于地面，采用前文所述遥控开关校准加速度计和陀螺仪的方式标定安装零偏，完成后查看上位机或手持遥控器中姿态角是否慢慢归0；<br>
（2）之后同样采用遥控开关校准方式触发磁力计校准，进入校准过程中蜂鸣器会1秒1次响同时LED为蓝灯闪烁，此时拿起飞行器进行旋转确保飞行器每个方向旋转一次后
继续水平旋转观差LED等是否退出蓝色闪烁模式，则标定完成。同样在远程端查看航向角是否符合当地实际朝向(航向偏差可能造成飞行器悬停打圈晃动)。<br>
完成校准后通过外八解锁查看电机转动情况确认符合安装要求，推动油门缺电机转速变化，下图以天地飞8通道遥控器为例给出一个常用的遥控器开关映射图。

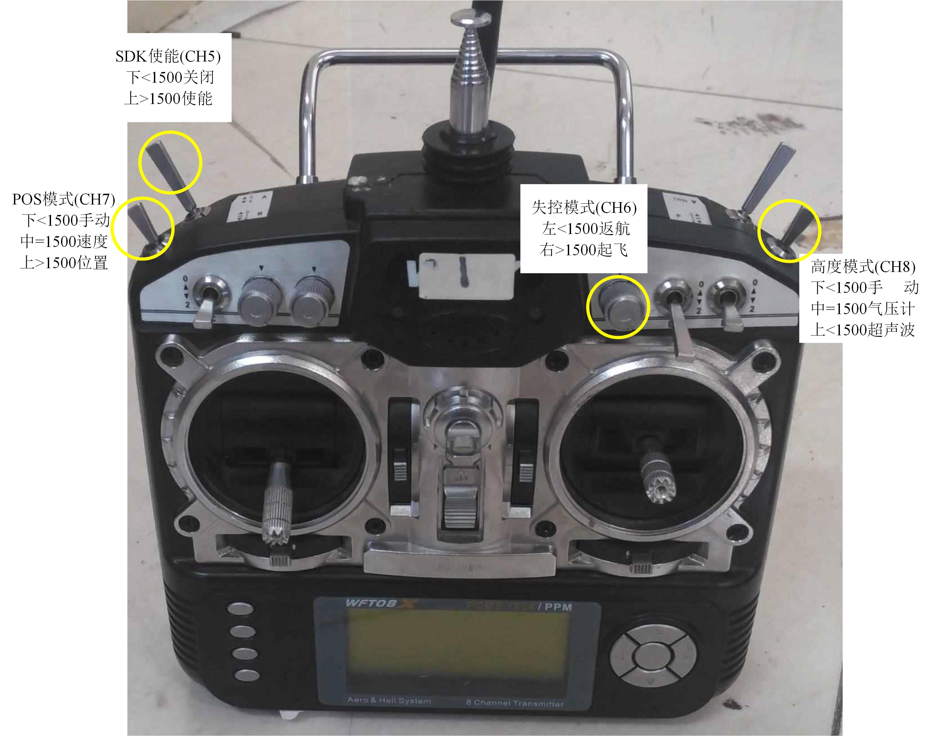
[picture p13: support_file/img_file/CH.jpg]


**注：如采用图中遥控配置：<br>**
(1)则高度档在上快速拨动POS档会触发磁力计校准，高度档在下快速拨动POS会触发加速度和陀螺仪校准；<br>
(2)SDK在上，失控在右，高度在中，位置在上(确认主状态机复位)，则解锁后油门到中位触发自动起飞和SDK飞行；<br>
(3)SDK飞行降落后，仅将失控拧到左，位置在下，SDK在下即可完成对状态机的复位；<br>
(4)飞行中失控从右旋转到左则进入失控保护策略；<br>

## 6.3 LED状态显示
____OLDX飞控板载三色LED能实现对飞控系统状态的基本情况查看，具体LED闪烁情况如下表所示：

LED闪烁|说明
-------------|-------------
红灯快闪|未连接遥控器
白色呼吸灯|飞控状态正常
蓝灯快闪|磁力计校准

## 6.4 手动飞行
____在完成飞控安装，电调顺序确认，电机转向缺人和飞行器参数配置，传感器校准后可以通过手动飞行模式缺参数是否合适，其具体步骤如下：<br>
(1)上电等待遥控连接白色呼吸灯<br>
(2)查看手持遥控器确认姿态角正确<br>
(3)确保高度模式和位置模式为手动状态<br>
(4)解锁飞行器，轻推油门确认电机转向正确<br>
(5)推到油门寻找飞行器起飞油门<br>
(6)在确保飞行器离地0.5米拨动遥杆，在上位机观察反馈数据或者目视观察控制参数是否合适<br>

## 6.5 定高飞行
____在完成手动飞行后可进行定高测试：<br>
(1)确保飞行器正常工作后切换气压定高模式<br>
(2)解锁飞行器后推动油门到中位以上，飞行器起飞切遥杆对应上下速度<br>
(3)在确保飞行器离地0.5米拨动遥杆，在上位机观察反馈数据或者目视观察控制参数是否合适<br>

## 6.6 位置悬停
在完成定高飞行后可进行位置悬停测试：<br>
(1)确保飞行器正常工作后切换气压定高模式<br>
(2)确保GPS定位星数满足6颗以上或者光流传感器连接且Qual大于150并且安装朝向正确<br>
(3)解锁后定高起飞<br>
(4)在确保飞行器离地0.5米后切换到速度模式，查看飞行器是否具有制动能力，切换到位置模式查看是否能满足0.2m内的悬停精度

## 6.7 航线飞行
____OLDX飞控移植了Mavlink通讯协议，目前支持与Qground地面站通信比进行航点设置，由于通讯协议还在完善因此目前只支持如下功能：<br>
(1)飞行器基础状态查看：姿态角、高度、GPS位置、GPS卫星数量、飞行器电量<br>
(2)航点写入<br>
<br>
正在更新的功能为：<br>
**(1)航点读出**<br>
**(2)自动起飞和RTL返航**<br>
(3)传感器校准<br>
(4)参数调节<br>

下面主要介绍航点参数写入操作：<br>
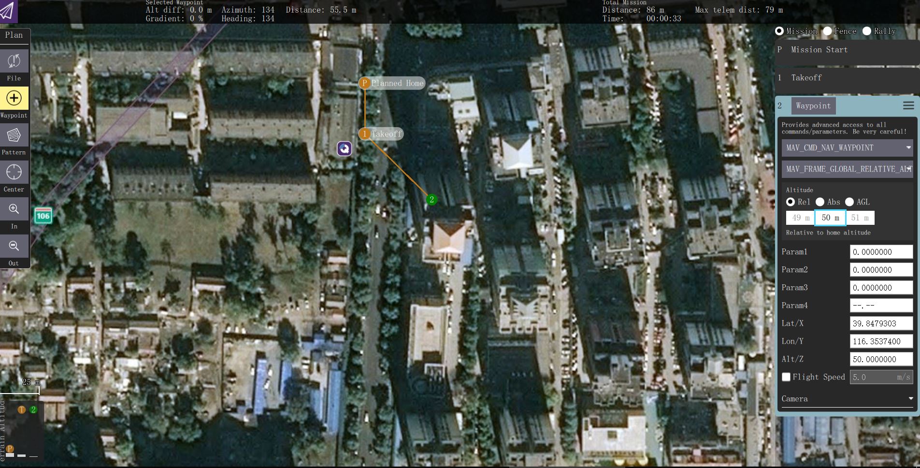
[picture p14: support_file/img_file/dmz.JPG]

<br>
各航点内相关参数说明如下：

参数|说明
-------------|-------------
Altitude|航点高度
Hold|航点停留时间
Heading|航点朝向
Acceptance|飞行速度 **(注：由于协议问题无法使用Flight Speed设置航点速度)**

____如要统一修改航线高度则先将第一个航点高度设置好后，后续添加航点高度将与其一致，写入航点后上位机会显示写入过程但由于通讯等问题可能
造成出现协议错误提示，此时取消后反复写入即可，如果航点写入正常则飞控会发出BB提示音，并可以在手持遥控器中SDK界面查看写入航点数量是
否一致。

## 6.8 SDK自主飞行
____SDK自主飞行时OLDX飞控相比目前市面上所有开源飞控最独特和最重要的功能，其旨在提供一个易于快速实现复杂控制逻辑和图像导航的编程方式，
后续将使用micropython作为SDK编程核心基于图形界面实现直观简单的SDK编程，其具体开发请参照第7小节内容，使能SDK飞行的具体过程如下：<br>
<br>
**(1)在飞行器宏定义中使用#define AUTO_MISSION，在Pos_ctrl.c文件中定义选用的SDK **<br>
(2)确认连接GPS或光流传感器<br>
**(3)在起飞前确认主状态机为IDLE**<br>
(4)遥控器开关使能SDK，打开位置模式和定高模式<br>
(5)解锁飞行器后推动油门到中位，确保其他遥感在中位则飞行器自动起飞并执行SDK飞行<br>
**(6)在飞行过程中可在手持遥控SDK界面实时观察自动任务执行情况，自主飞行中可通过遥控操作打断飞行或者使用失控反航**

# 7 进阶SDK开发说明
## 7.1 主状态机书写
____SDK开发只需要完成主状态机框架书写和SDK调用即可，在oldx_mission.c中定义你的SDK程序并在pos_ctrl.c中进行调用，具体的SDK框架如下：

```
u8 mission_test(float dt)
{ 
	u8 flag=0,mission_finish=0,temp=0;
	static float mission_time;

	switch(mission_state){
	case 0:
			   flag=take_off_task1(2,1.5,dt);
		   break;
	case 1:
			   flag=set_drone_z_task(5.5,dt);
	       break;
	case 2:mission_finish=1;
	       break;
	default:break;
	}
	
	if(flag)
		mission_state++;
	
	mission_time+=dt;
	
	if(mission_finish)
	  return 1;		
  else
      return 0;		
}	

```

上段代码给出了一个简单的自动起飞后悬停在5.5米高度的SDK程序。SDK以一个状态机进行驱动，每个状态中通过调用API使得flag为1表示该子
任务完成实现对状态标志为mission_state的向前推动，同一个状态下可以进行多个任务但需要保证flag由谁进行触发，同时也可不使用API完成的判断
自己设计状态跳转条件，状态跳转也可以不采用顺序进行对mission_state直接赋值实现特殊状态处理，该文件下给出了多个Demo实例，可参照其进行修改
实现SDK开发。

## 7.2 SDK介绍
这里给出目前版本中支持的API函数输入和输出详细说明：<br>

set_pos_task|设置飞行器全局目标位置
-------------|-------------
x,y,z|全局坐标系位置（米），如某个参数为0则保持当前该轴位置
完成条件|全局位置误差小于WAY_POINT_DEAD

<br><br>

way_point_task|设置飞行器GPS目标位置
-------------|-------------
lat,lon,height|GPS期望位置，如某个参数为0则保持当前该轴位置
loter_time|该航点悬停时间
mode|mode==MODE_FAST_WAY 则为快速飞行模式(放大对航点控制误差的判断条件)
完成条件|目标误差小于WAY_POINT_DEAD1并保证持续MISSION_CHECK_TIME时间

<br><br>

way_point_mission|航线飞行
-------------|-------------
spd_limit|总体航向速度限制(每个航点速度可在上位机中accpentance进行设置如其为0则使用该参数限制飞行速度)
head_to_waypoint|为1则机头朝向每个航点
mode|mode==MODE_FAST_WAY 则为快速飞行模式(放大对航点控制误差的判断条件)
完成条件|经过所有航点

<br><br>

return_home|返航
-------------|-------------
set_z|返航高度
spd_limit|速度限制
en_land|为1则返航后直接执行自动降落
head_to_home|机体朝向返航点
完成条件|完成返航任务

<br><br>

spd_move_task|机体下给定速度
-------------|-------------
x,y,z|给定速度，如为0则该轴保持当前位置
time|给定速度持续时间
完成条件|达到设定时间

<br><br>

pos_move_global_task|在全局坐标系下向前后左右移动距离
-------------|-------------
x,y,z|移动距离
完成条件|达到设定位置

<br><br>

pos_move_body_task|在机体坐标系下向前后左右移动距离
-------------|-------------
x,y,z|移动距离
完成条件|达到设定位置

<br><br>

pan_set_task|控制云台俯仰角度
-------------|-------------
pitch|设定角度
完成条件|无

<br><br>

pan_search_task|云台上下搜索API
-------------|-------------
min|最小角度
max|最大角度
da|角度增量
en_yaw|为1则搜索中航向也会左右反复搜索
en_forward|为1则每次完成一次反复搜索后向前以0.3m/s的速度前进
完成条件|无

<br><br>

down_ward_search_task|圆环轨迹搜索
-------------|-------------
r|圆轨迹半径
z|飞行高度
d_angle|圆形轨迹角度增量  
d_r|半径增量
完成条件|无

<br><br>

down_ward_search_task_tangle|蛇形航点轨迹规划
-------------|-------------
w|规划轨迹宽度航点数量
h|规划轨迹长度航点数量
wn|宽度间隔距离  
hn|长度间隔距离
spd_limit|飞行速度限制
z|飞行高度
完成条件|经过所有航点

<br><br>

target_track_downward_task|下置相机目标跟踪
-------------|-------------
target|目标图像信息结构体
spdz|下降速度
end_z|下降停止高度  
mode|模式 MODE_SPD：使用像素偏差  MODE_POS：使用估计的全局位置
完成条件|达到下降高度

<br><br>

target_track_pan_task|前置云台目标跟踪
-------------|-------------
target|目标图像信息结构体
close_param|速度模式下为云台最小角度  位置模式下为离目标距离
en_pitch|使能云台俯仰轴对准  
en_yaw|使能飞行器航向对准
close_mode|模式 MODE_SPD：使用像素偏差  MODE_POS：使用估计的全局位置
完成条件|云台达到目标角度或飞行器离目标距离达到设定值

<br><br>

avoid_task|自主避障
-------------|-------------
target|目标图像识别结果
set_x|期望前进X轴速度
set_y|期望前进Y轴速度
set_z|NC
dead|速度死区
max_spd|最大避障速度
完成条件|

<br><br>

avoid_way_point_task|航点自主避障
-------------|-------------
target|目标图像识别结果
tar_lat|目标经度
tar_lon|目标维度
spd|前进速度
dead|速度死区
max_spd|最大避障速度
mode|模式NC
完成条件|达到目标位置

<br><br>

set_drone_yaw_task|设置飞行器航向
-------------|-------------
yaw|目标航向角
rate_limit|旋转速度限制
完成条件|达到目标角度

<br><br>

set_drone_z_task|设置飞行器高度
-------------|-------------
z|目标高度
完成条件|达到目标高度

<br><br>

aux_open|辅助通开关设置
-------------|-------------
sel|辅助通道
open|开关
完成条件|

<br><br>

land_task1|降落
-------------|-------------
spd|下降速度
完成条件|达到触地检测标准

<br><br>

delay_task|空闲等待
-------------|-------------
delay|等待时间(秒)
完成条件|达到等待时间

<br><br>

draw_heart|光滑爱心图案
-------------|-------------
time|飞行总时间(秒)
size|爱心尺寸(米)
完成条件|达到等待时间

## 7.3 常用SDK解析
### 7.1 自动起飞->航线飞行->自动返航
____该SDK为最常用的任务架构，通过在其中添加打断航线飞行的状态判断能快速地实现飞行中对目标识别
触发的跟踪，或者飞行中看到降落标志触发的自动降落。

```
u8 takeoff_mission_return(float dt)
{ 
	u8 flag=0,mission_finish=0,temp=0;
	static float mission_time;

	switch(mission_state){
	case 0:
			   flag=take_off_task1(5,1.5,dt);//自动起飞以1.5m/s的速度到达5m高度
		   break;
	case 1:
			   flag=delay(2,dt);//在该高度等待2s
	       break;
    case 2:
			   flag=way_point_mission(2,NEN_HEAD_WAY,dt);//以2m/s的速度进行航向飞行期间航向角为航点设定角度
		   break;
	case 3:
			   flag=return_home(15,2,EN_LAND,NEN_HEAD_WAY,dt);//以2m/s的速度从15m的高度反航，进行航向飞行期间航向角为航点设定角度并直接降落
	break;
	case 4:mission_finish=1;
	       break;
	default:break;
	}
	
	if(flag)
		mission_state++;
	
	mission_time+=dt;
	
	if(mission_finish)
	  return 1;		
  else
      return 0;		
}	

```
### 7.2 自动起飞->区域搜索->自动返航
____该SDK是IMAV比赛中一个项目，项目要求如下：起飞前给定参赛选手5分钟前一个伤员的经纬度，无人机需要自主飞行到
该区域上方基于图像信息判断伤员位置，并将舵机挂钩上的医疗箱投递到伤员5m的半径内，之后自动返航并基于图像精确
降落在起飞点1m内。

```
float lat_human,lon_human;//寻找找伤员的经纬度
u8 mission_search1(float dt)
{ 
	u8 flag=0,mission_finish=0,temp=0;
	float dis=0;
	static float mission_time;
	switch(mission_state){
	case 0:flag=take_off_task1(2,1.5,dt);//自动起飞 
		    break;
	case 1:pan_set_task(90,dt);//云台向下
		   flag=set_drone_z_task(6,dt);//达到起飞高度6m
		     mission_time=0;
		     break;	
  case 2:  mode_oldx.sdk_flag=1;//切换图像识别为伤员      
		   flag=way_point_mission(1.6,NEN_HEAD_WAY,dt);//开始航线飞行
	       if(c2c.connect&&c2c.x<160+90&&c2c.x>160-90&&c2c.y<120+90&&c2c.y>120-90)//识别到伤员
				   cnt_task[5]++;
				 
		   if(cnt_task[5]>20&&cnt_task[6]==0)//切换到目标对准
		  {mission_state=102;cnt_task[0]=cnt_task[1]=cnt_task[2]=cnt_task[5]=flag=0;}
		     break;
	case 3://在给定经纬度未找到目标则规划蛇形航线进行搜寻
				 mode_oldx.sdk_flag=1;
				 flag=down_ward_search_task_tangle(10,10,3,3,0.6,7.5,dt);
				 if(c2c.connect&&c2c.x<160+90&&c2c.x>160-90&&c2c.y<120+90&&c2c.y>120-90)//找到伤员
					 cnt_task[5]++;
				 
				 if(cnt_task[5]>6&&cnt_task[6]==0)//找到伤员切换对准状态
					{mission_state=102;cnt_task[0]=cnt_task[1]=cnt_task[2]=flag=0;}
					
				 if(flag&&cnt_task[6]==0)//搜寻完毕后重复直到超时
				  {mission_state=2;cnt_mission[MISSION_CNT]=cnt_task[5]=cnt_task[0]=cnt_task[1]=cnt_task[2]=flag=0;}
					
				 if(cnt_task[6]==1)//完成投递则返航
					 flag=1;
	       break;
  //------------------------------------------------------
	case 4:flag=return_home(12,2,NEN_LAND,NEN_HEAD_WAY,dt);//返航
				 if(flag)
					cnt_task[0]=cnt_task[1]=cnt_task[2]=0;
	       break;
	case 5:flag=set_drone_z_task(6,dt);//达到识别降落标志最佳高度
				 break;
	case 6:mode_oldx.sdk_flag=0;//切换图像识别为降落标志
				 flag=target_track_downward_task(&c2c,0.4,0.66,MODE_SPD,dt);//使用下置相机对准降落标志
				 if(c2c.check)
				  cnt_task[0]=0;
				 else
				  cnt_task[0]++;
				 
				 if(cnt_task[0]>10/dt)//降落过程中一直未找到目标则切换搜索模式
				 {mission_state=11;cnt_task[0]=cnt_task[1]=cnt_task[2]=0;
				 cnt_mission[C_SEARCH_T_INT]=cnt_mission[C_SEARCH_T_INT1]=flag=0;}
				
				 if(cnt_task[1]++>15/dt)
				 {flag=1;cnt_task[0]=cnt_task[1]=0;}
				 break;
	case 7:mode_oldx.sdk_flag=0;
				 flag=target_track_downward_task(&c2c,0.25,0.66,MODE_SPD,dt);
	       break;
	case 8:flag=land_task1(LAND_SPD,dt);//垂直降落
	       break;
	case 9:mission_finish=1;
	       break;
	//-----------------------AUX MISSION----------------------------
	case 11://搜索降落标志
	      mode_oldx.sdk_flag=0;//
	      flag=down_ward_search_task_tangle(8,8,4,4,0.4,5,dt);//tangle
			  if(c2c.check)
					 cnt_task[0]++;
				
				if(cnt_task[0]>5)
					{cnt_task[0]=0;mission_state=6;flag=0;}
					
				if(cnt_task[2]++>60/dt||flag)
				{mission_state=12;cnt_task[2]=0;flag=0;}
	      break;
	case 12://搜索一边仍未找到降落标志则直接返航使用起飞点经纬度自动降落
			 if(return_home(4,0.8,NEN_LAND,NEN_HEAD_WAY,dt))
					mission_state=7;
			 break;		 	 			
	case 13://航线飞行			
				flag=way_point_mission(1,NEN_HEAD_WAY,dt);	
        if(flag)
				{flag=0;aux_open(2,1);mission_state=4;}					
	break;			
	//--------------------
	case 102://对准伤员 达到设定高度后投递医疗包
		    mode_oldx.sdk_flag=1;//
		    flag=target_track_downward_task_search(&c2c,0.25,4.5,dt);
				if(cnt_task[2]++>30/dt)
				{mission_state=3;cnt_task[2]=flag=cnt_task[5]=0;}
				
				if(flag)//投递货物
				{mission_state=4;//to return home
				 cnt_task[2]=flag=0;
				 aux_open(2,1);
				 cnt_task[6]=1;//drop flag
				}
	      break;
				
	default:break;
	}

	if(flag)
		mission_state++;
	
	mission_time+=dt;
	if(mission_time>3*60&&(mission_state>=100||mission_state==3))//任务超时则自动返航
	{mission_state=13;cnt_mission[C_SEARCH_T_INT]=cnt_mission[C_SEARCH_T_INT1]=0;}
	
	if(mission_finish)
	  return 1;		
  else
    return 0;		
}	
```

### 7.3 自动起飞->激光雷达避障->自主返航
____该SDK是IMAV比赛中一个项目，项目要求如下：起飞前给定参赛选手5分钟前一个伤员的经纬度，无人机需要资助飞行到
该区域但与7.2不同的时目标处于密集树林内，因此需要在搜寻时能自动躲避障碍物，则使用2D激光雷达得到飞行器避障速度
进行前进搜索中不但躲避树木。

```

u8 mission_avoid(float dt)
{ 
	u8 flag=0,mission_finish=0,temp=0;
	float lat,lon;
	static float mission_time;
	pan_set_task(90,dt);
	float dis=0;
	switch(mission_state){
	case 0:
			   flag=take_off_task1(1.68,1.5,dt);//自动起飞
		    break;
	case 1:
				 pan_set_task(90,dt);
				 flag=set_drone_z_task(1.68,dt);//达到1.6m悬停
				 lat=navData.missionLegs[LIMIT(navData.Leg_num-1,0,99)].targetLat;//给定经纬度
				 lon=navData.missionLegs[LIMIT(navData.Leg_num-1,0,99)].targetLon;
				 mission_time=0;
		     break;	
	case 2:
		     mode_oldx.sdk_flag=1;//图像切换伤员识别
		     set_drone_z_task(1.5,dt);//期望仿地飞行搜索高度
			 flag=avoid_way_point_task(&c2c,lat,lon,0.25,0.2,0.5,0,dt);
			 
			 if(c2c.check)
			  cnt_task[0]++;
			 
			  if(cnt_task[0]>5){//投递货物
				  aux_open(2,1);
				  flag=1;
				}
	       break;	
	case 3:return_home(10,2,EN_LAND,NEN_HEAD_WAY,dt);//自动返航
	       break;					
	default:break;
	}
	
	if(flag)
		mission_state++;
	
	mission_time+=dt;
	if(mission_time>7*60&&(mission_state>100||mission_state==2))//超时返航
		mission_state=3;
	
	if(mission_finish)
	  return 1;		
  else
    return 0;		
}	
```

# 8 捐赠与项目后续开发计划
____如果您觉得该项目对您有帮助，也为了更好的项目推进和软硬件更新，如果愿意请通过微信捐赠该项目！


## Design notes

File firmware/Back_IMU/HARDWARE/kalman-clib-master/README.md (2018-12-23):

# Kalman Filter C Implementation #

Microcontroller targeted naive Kalman filter implementation in pure C using code ported from the [Efficient Java Matrix Library](https://code.google.com/p/efficient-java-matrix-library).

### License

The project is licensed under the **MIT license**, a copy of which can be found in [LICENSE.md](LICENSE.md).

## Implemented so far ##
* Memory-optimizing preprocessor based Kalman Filter factory
* Algorithmically optimized matrix/matrix and matrix/vector operations
* Matrix inverse using Cholesky decomposition

## Example filters ##
* Gravity constant estimation using only measured position

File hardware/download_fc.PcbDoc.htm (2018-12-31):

Altium Reporting Options

# File in Previous Format

Date | : | 2018/12/30
Time | : | 16:22:11
Filename | : | D:\FC1\OLDX_Fly_Controller\hardware\download_fc.PcbDoc

Version | Warning
Summer 09 | CAUTION - File contains old violation objects. These violations are no longer supported & will not be loaded.Please run DRC after opening this file in order to refresh the violations.
Summer 09 | CAUTION - Existing testpoint rules and settings are used as fabrication testpoint information.

This file was generated by an earlier version of the software

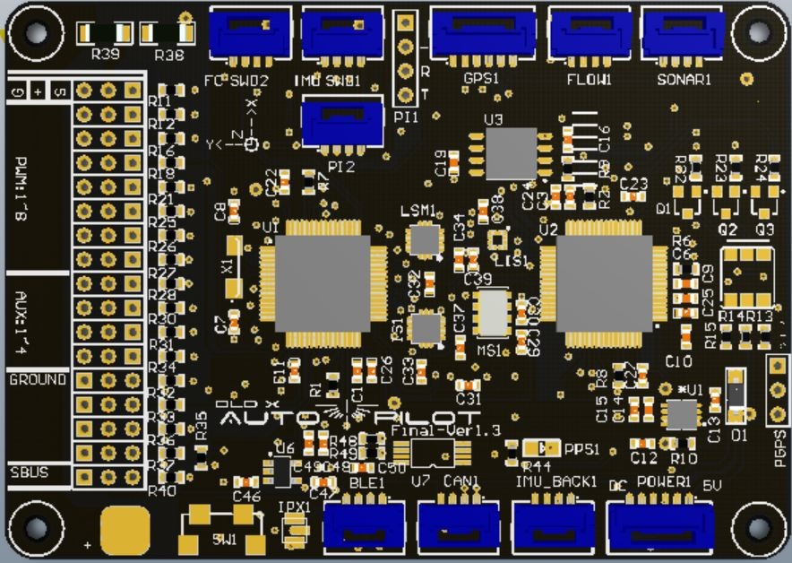
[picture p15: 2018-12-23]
support_file/img_file/pcb_fc.JPG

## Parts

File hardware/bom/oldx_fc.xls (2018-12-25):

Comment | Description | Designator | Quantity
AS1364-BTDT-33 |  | *U1 | 1
XH414 | XH414 IV01E | BAT2 | 1
2.2UF | 贴片电容0603 | C1, C2, C3, C4 | 4
10NF | 贴片电容0603 | C5, C6, C14 | 3
20PF | 贴片电容0603 | C7, C8, C9, C10 | 4
0.1UF | 贴片电容0603 | C11, C12, C16, C17, C18, C20, C21, C22, C23, C24, C25, C26, C27, C30, C31, C32, C33, C34, C37, C39, C42, C50 | 22
4.7uf | 贴片电容0603 | C13, C15, C29 | 3
1UF | 贴片电容0603 | C19, C35, C36, C40, C41, C43, C46, C49 | 8
100uF | 贴片电容0603 | C28 | 1
100nF | 贴片电容0603 | C38 | 1
223 | 贴片电容0603 | C47 | 1
104 | 贴片电容0603 | C48 | 1
IN4733 5.1V | 贴片稳压二极管 | D1 | 1
BAT54WS | 单肖特基二极管 | D7 | 3
Header 6 | 卧贴端子 | GPS1, POWER1 | 2 | https://item.taobao.com/item.htm?spm=a1z09.2.0.0.MJL2ZN&id=528744124006&_u=o1klsj899edd
IPEX | IPEX座 | IPX1 | 1
ICM20602 |  | IS1 | 1
5050 RGB | 三色LED | LEDRGB1 | 1 | 焊接时LED三角在封装竖线对侧
LIS3MDL |  | LIS1 | 1
LSM6DS33 |  | LSM1 | 1
MS5611 | Sensor | MS1 | 1
LED |  | PPS1 | 1
S8050 | 8050/BCW846/BCW847 | Q1, Q2, Q3, Q4 | 4
10K | 贴片电阻 | R1, R2, R5, R6, R7, R8, R9, R17, R35, R42 | 10
4.7K | 贴片电阻 | R3, R4, R48, R49 | 4
1K | 贴片电阻 | R10, R11, R12, R16, R18, R19, R20, R21, R22, R23, R24, R25, R26, R27, R28, R30, R31, R32, R33, R34, R36, R37, R40, R41 | 24
100R | 贴片电阻 | R13, R14, R15 | 3
120R | 贴片电阻 | R29, R45, R46, R47 | 4
0R | 贴片电阻 | R38,R41 | 2
510R | 贴片电阻 | R44 | 1
SW-PB1 | 侧贴按键 | SW1 | 1
STM32F405RGT6 | 单片机 | U1, U2 | 2
W25X16 | Flash芯片 | U3, U5 | 2
TJA1050 |  | U4 | 1
RT9193-33 | 3.3V超低压差LDO | U6 | 1
24C32 | EEPROM | U7 | 1
 |  |  | 1
8MHZ | 贴片无源晶振 | X1, X2 | 2
Header 4 | 卧贴端子 | BLE1, CAN1, FLOW1, IMU_BACK1, SONAR1, SWD1, SWD2 | 7 | https://item.taobao.com/item.htm?spm=a1z09.2.0.0.MJL2ZN&id=528744124006&_u=o1klsj899edd
Header 4 | 立贴端子 | PI2, | 1 | https://item.taobao.com/item.htm?spm=a1z09.2.0.0.MJL2ZN&id=528744124006&_u=o1klsj899edd
2.4G射频芯片 |  | https://item.taobao.com/item.htm?spm=a1z09.2.0.0.3d9c2e8dfeAuPP&id=45719116718&_u=n1klsj8974f5
3Pin 2.54弯排针

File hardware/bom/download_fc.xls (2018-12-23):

Comment | Description | Designator | Footprint | Quantity
0.1UF | Capacitor | C1 | C0603 | 1
1N4148 | 二极管 | D1 | 1n4148-SOD123 | 1
10K | 0603 | R1, R2 | R0603 | 2
MicroUSB口 |  | ST_Link_1 | USB/SM0.8-6H5_M | 1
4P卧贴 | Header, 4-Pin | SWD1 | JST_GH_V4 | 1 | https://item.taobao.com/item.htm?spm=a1z09.2.0.0.MJL2ZN&id=528744124006&_u=o1klsj899edd

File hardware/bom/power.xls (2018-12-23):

Comment | Description | Designator | Footprint | Quantity
BAT54WS | 单肖特基二极管 | D1, D3 | SOD-323 | 2
IN4733 5.1V | Zener Diode | D2 | 1n4148-SOD123 | 1
稳压模块5V | Header, 4-Pin | DCDC1 | HDR1X4 | 1 | https://detail.tmall.com/item.htm?id=581519703330&spm=a1z09.2.0.0.e0c32e8dqo1Tlc&_u=n1klsj89a304
蜂鸣器 |  | DET1 | BEEP | 1 | https://item.taobao.com/item.htm?id=557399448031&ns=1&abbucket=8
4P卧贴端子 | Header, 4-Pin | LINK1, LINK2 | JST_GH_V4 | 2 | https://item.taobao.com/item.htm?spm=a1z09.2.0.0.MJL2ZN&id=528744124006&_u=o1klsj899edd
HEAD2 |  | P1 | HEADER2-1.25MM | 1
6P卧贴端子 | Header, 6-Pin | POWER1 | JST_GH_V6 | 1
S8050 | 8050/BCW846/BCW847 | Q1 | SOT-23R | 1
1K | 0603 | R1 | R0603 | 1
10K | 0603 | R2 | R0603 | 1

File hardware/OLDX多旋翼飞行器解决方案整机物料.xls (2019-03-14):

 | 参数 | 采购方式 | 数量 | 单价 | 地址
飞控电子设备
飞控 | OLDX | 加工 | 1 |  | https://github.com/golaced/Oldx_fly_controller
降压模块 | OLDX | 加工 | 1 |  | https://github.com/golaced/Oldx_fly_controller
手持监视器 | OLDX | 加工 | 1 |  | https://github.com/golaced/Oldx_fly_controller
下载器 | OLDX | 加工 | 1 |  | https://github.com/golaced/Oldx_fly_controller
3D打印外壳 | OLDX | 加工 | 1 |  | https://github.com/golaced/Oldx_fly_controller
下载器转接板 | OLDX | 加工 | 1 |  | https://github.com/golaced/Oldx_fly_controller
MicroUSB线 |  | 淘宝采购 | 1 | 9.9 | https://buyertrade.taobao.com/trade/itemlist/list_bought_items.htm
端子线4P |  | 淘宝采购 | 4 | 1 | https://item.taobao.com/item.htm?spm=a1z09.2.0.0.1dfd2e8dThfKeF&id=528691263571&_u=e1klsj89840e
端子线6P |  | 淘宝采购 | 1 | 1 | https://item.taobao.com/item.htm?spm=a1z09.2.0.0.1dfd2e8dThfKeF&id=528691263571&_u=e1klsj89840e
GPS | 乐迪mini | 淘宝采购 | 1 | 110 | https://item.taobao.com/item.htm?spm=a1z09.2.0.0.43ea2e8dNQewOJ&id=561369249119&_u=e1klsj8971d3
GPS支架 | 折叠 | 淘宝采购 | 1 | 13 | https://item.taobao.com/item.htm?spm=a1z09.2.0.0.43ea2e8dNQewOJ&id=521550953806&_u=e1klsj89a178
NRF芯片 |  | 淘宝采购 | 2 | 30 | https://item.taobao.com/item.htm?spm=a1z09.2.0.0.43ea2e8dNQewOJ&id=45719116718&_u=e1klsj89f06d
NRF天线 |  | 淘宝采购 | 2 | 1 | https://item.taobao.com/item.htm?spm=a1z09.2.0.0.43ea2e8dNQewOJ&id=524223974321&_u=e1klsj890454
监视器电源线 |  | 淘宝采购 | 2 | 1 | https://item.taobao.com/item.htm?spm=a1z09.2.0.0.43ea2e8dNQewOJ&id=39955787073&_u=e1klsj89e637
监视器遥控帽 |  | 淘宝采购 | 1
监视器OLED |  | 淘宝采购 | 1 | 43 | https://detail.tmall.com/item.htm?id=41844085048&spm=a1z09.2.0.0.1dfd2e8dThfKeF&_u=e1klsj8977cf
监视器电池 | 3.7 800mah | 淘宝采购 | 1 | 25 | https://item.taobao.com/item.htm?spm=a1z09.2.0.0.1dfd2e8dThfKeF&id=43805798084&_u=e1klsj8910f0
飞行器
机架 | 330轴距 | 淘宝采购 | 1 | 80 | https://item.taobao.com/item.htm?id=41151005596&ns=1&abbucket=20
电调 | 15A 好赢乐天 | 淘宝采购 | 4 | 36 | https://item.taobao.com/item.htm?spm=a1z09.2.0.0.43ea2e8dNQewOJ&id=41159174305&_u=e1klsj899a7c
电机 | 1500kV EMAX | 淘宝采购 | 4 | 88 | https://item.taobao.com/item.htm?id=522211990287&ns=1&abbucket=20
电池 | 2200mah 3S T差 | 淘宝采购 | 1 | 75 | https://item.taobao.com/item.htm?spm=a1z09.2.0.0.43ea2e8dNQewOJ&id=561469537882&_u=e1klsj899b4c
桨叶 | APC8038 | 淘宝采购 | 4 | 6 | https://item.taobao.com/item.htm?id=35858085148&ns=1&abbucket=20
充电器 | B6平衡充 | 淘宝采购 | 1 | 180
遥控器 | 天地飞 美国手 | 淘宝采购 | 1 | 480 | https://item.taobao.com/item.htm?spm=a1z09.2.0.0.43ea2e8dNQewOJ&id=18313212887&_u=e1klsj89c3f7
接收机 | 天地飞miniWbus | 淘宝采购 | 1 | 82 | https://item.taobao.com/item.htm?spm=a1z09.2.0.0.43ea2e8dNQewOJ&id=37606241076&_u=e1klsj891cec
保护圈 |  | 淘宝采购 | 1
T插头 |  | 淘宝采购 | 2
电源线 |  | 淘宝采购 | 2
舵机延长线 |  | 淘宝采购 | 4
香蕉头 |  | 淘宝采购 | 12

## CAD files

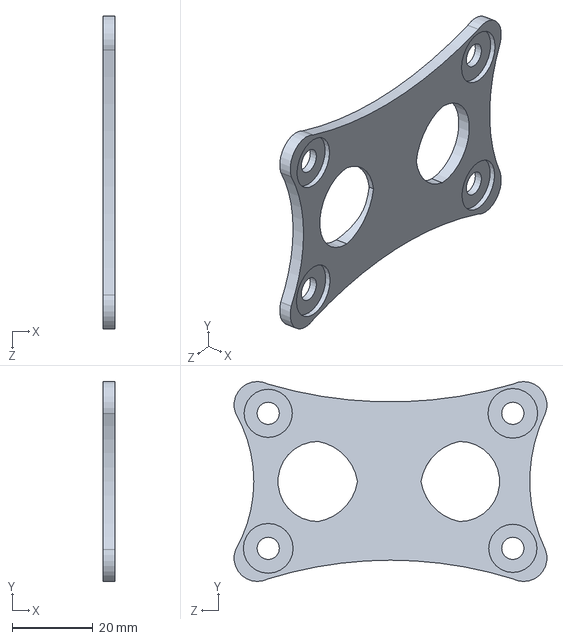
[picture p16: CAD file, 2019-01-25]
hardware/3D print/fc_cap3.SLDPRT
3.00 x 49.4 x 77.3 mm

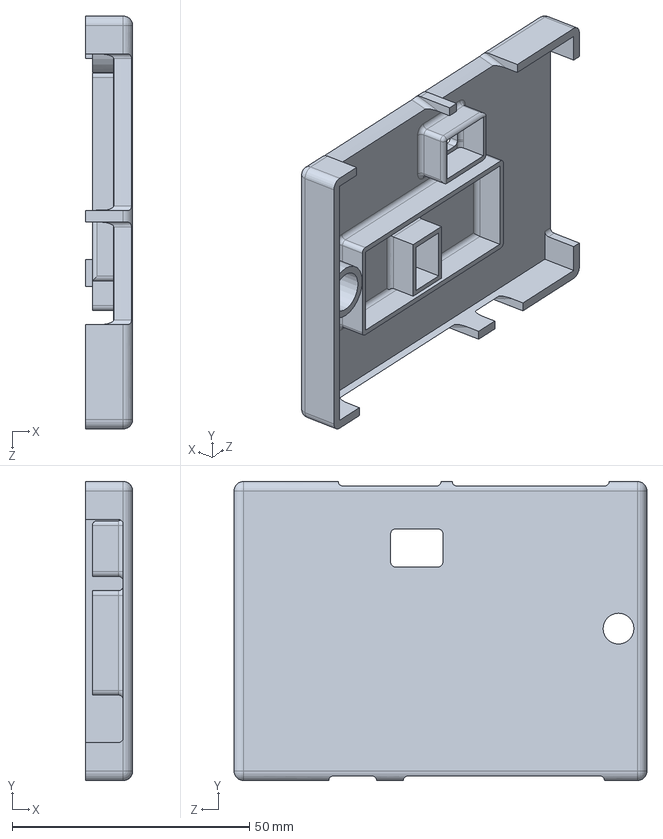
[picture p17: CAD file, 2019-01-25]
hardware/3D print/fc_cap2.SLDPRT
10.0 x 63.0 x 87.0 mm

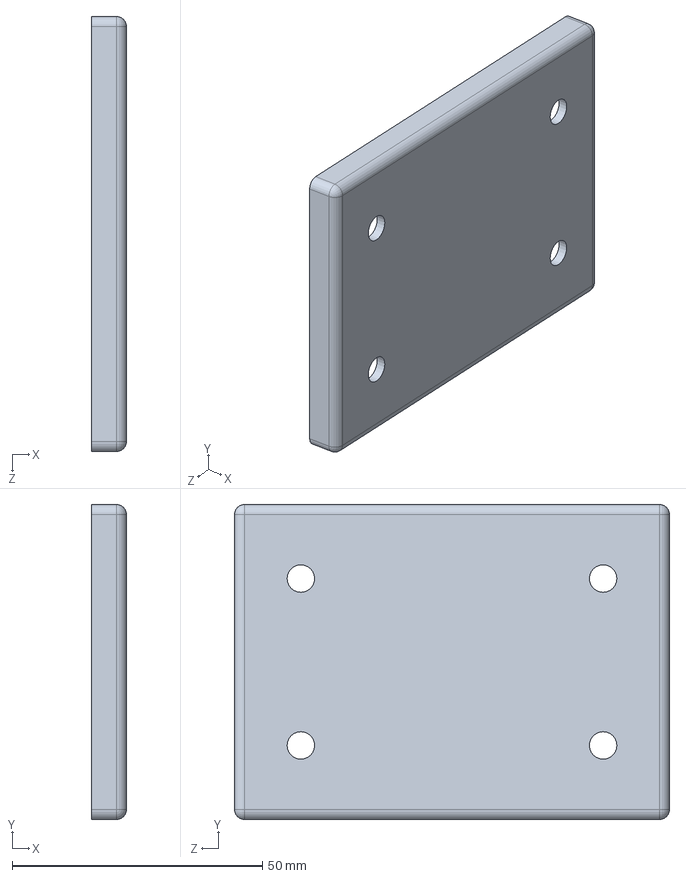
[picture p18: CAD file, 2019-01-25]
hardware/3D print/fc_cap1.SLDPRT
7.00 x 63.0 x 87.0 mm

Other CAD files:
hardware/3D print/fc_cap1.STL
hardware/3D print/fc_cap2.STL
hardware/3D print/fc_cap3.STL

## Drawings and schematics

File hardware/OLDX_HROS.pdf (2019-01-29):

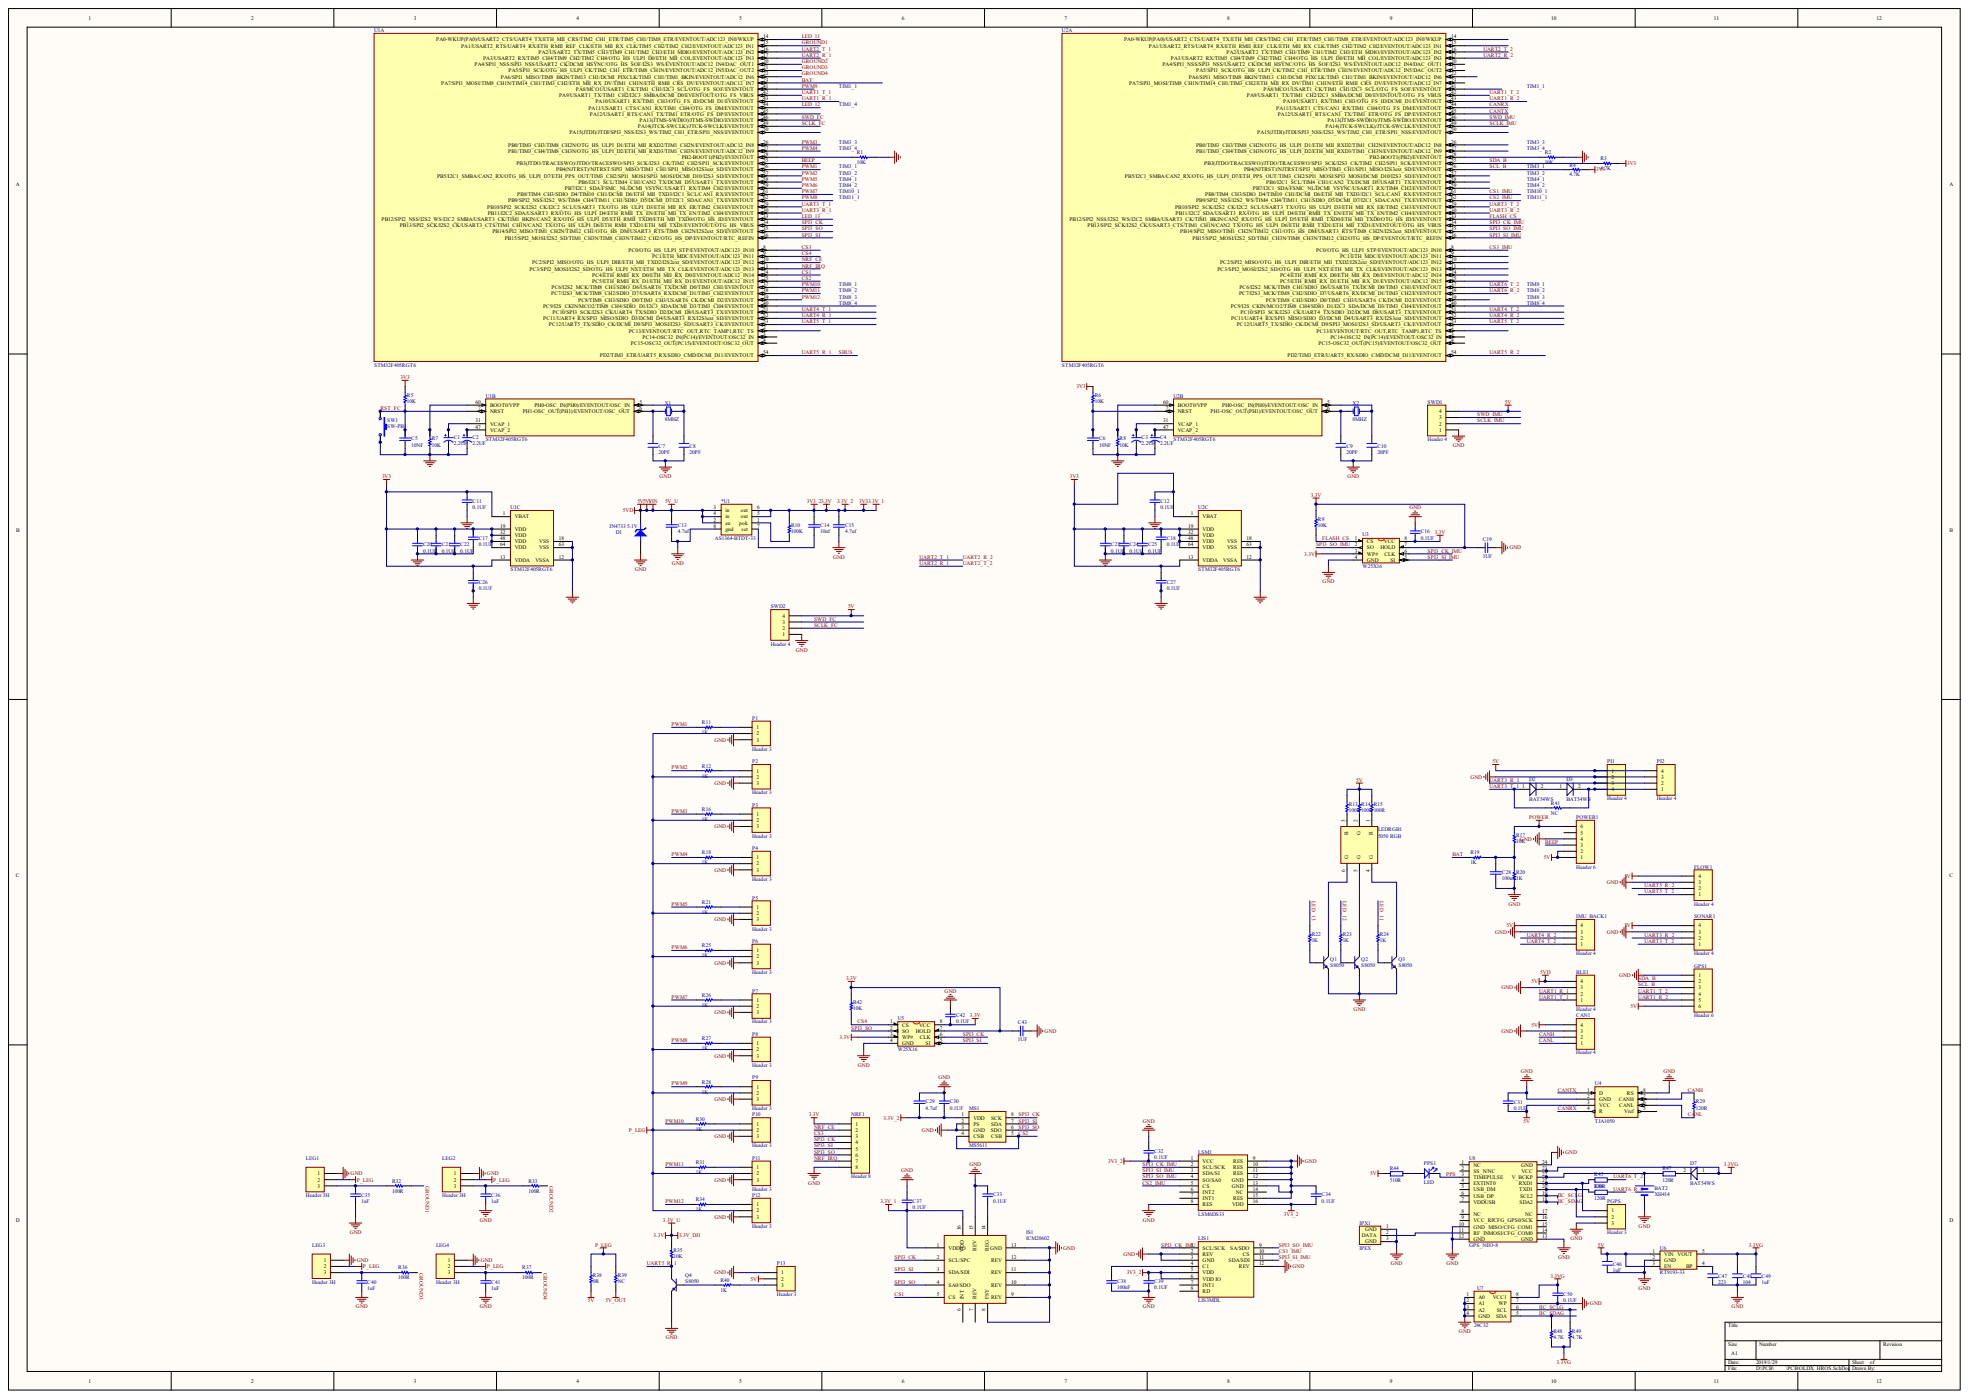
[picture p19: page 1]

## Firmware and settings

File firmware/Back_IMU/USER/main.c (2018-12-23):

#include "include.h" 
#include "iic_soft.h"
#include "iic_imu1.h"
#include "iic2.h"
#include "hml_sample.h"
#include "ms5611.h"
#include "alt_kf.h"
#include "flash.h"
#include "led_fc.h"
#include "bmp_adc.h"
#include "flash_w25.h"
#include "ucos_ii.h"
#include "os_cpu.h"
#include "os_cfg.h"
#include "ucos_task.h"
#include "dog.h"
#include "ukf_task.h"
#include "stm32f4xx_dma.h"
#include "LSM303.h"
#include "Soft_I2C_PX4.h"
#include "LIS3MDL.h"
#include "nav_ukf.h"
#include "gps.h"
 /////////////////////////UCOSII启动任务设置///////////////////////////////////
//START 任务
//设置任务优先级
#define START_TASK_PRIO      			20 //开始任务的优先级设置为最低
//设置任务堆栈大小
#define START_STK_SIZE  				64
//任务堆栈	
OS_STK START_TASK_STK[START_STK_SIZE];
//任务函数
void start_task(void *pdata);	
//////////////////////////////////////////////////////////////////////////////
    
OS_EVENT * msg_key;			//按键邮箱事件块	  
OS_EVENT * q_msg;			//消息队列

OS_FLAG_GRP * flags_key;	//按键信号量集
void * MsgGrp[256];			//消息队列存储地址,最大支持256个消息
SYSTEM module;
uint16_t cpuGetFlashSize(void)
{
   return (*(__IO u16*)(0x1FFF7A22));
}

//读取ChipID
u32 mcuID[3];
void cpuidGetId(void)
{
    mcuID[0] = *(__IO u32*)(0x1FFF7A10);
    mcuID[1] = *(__IO u32*)(0x1FFF7A14);
    mcuID[2] = *(__IO u32*)(0x1FFF7A18);
}

float ekf_loop_time1;
int main(void)

{ 
	NVIC_PriorityGroupConfig(NVIC_GROUP);//设置系统中断优先级分组2
	delay_init(168);  //初始化延时函数
	Initial_Timer_SYS();
	LED_Init();								//LED功能初始化
	Delay_ms(100);
	//-------------------------Para Init------------------------------------	
	W25QXX_Init();			//W25QXX初始化
	READ_PARM();//读取参数
	Delay_ms(4000);
  IIC_IMU1_Init();

	#if IMU_UPDATE
	LIS3MDL_enableDefault();
	Delay_ms(10);						//延时
	#endif
	Drv_GpsPin_Init6();
	Delay_ms(500);
//------------------------Uart Init-------------------------------------
	#if USE_OUTER_LINK
	Usart1_Init(57600);			//Outer Linker
	#else
	Drv_GpsPin_Init();
	#endif
	
	#if EN_DMA_UART1 
	MYDMA_Config(DMA2_Stream7,DMA_Channel_4,(u32)&USART1->DR,(u32)SendBuff1,SEND_BUF_SIZE1+2,1);
	#endif
	Usart2_Init(576000L);			//IMU_LINK
	#if EN_DMA_UART2
	MYDMA_Config(DMA1_Stream6,DMA_Channel_4,(u32)&USART2->DR,(u32)SendBuff2,SEND_BUF_SIZE2+2,1);
	#endif
	#if defined(USE_WIFI_CONTROL)
	Usart4_Init(19200);
	#else
		#if USE_LASER_AVOID
		Usart4_Init(576000L);     //AVOID BOARD
		#else
			#if USE_M100_IMU
			Usart4_Init(115200L);     //IMU2 Link
			#else
			Usart4_Init(576000L);     //PI FLOW
			#endif
		#endif
	#endif
	#if USE_IMU_BACK_IO_AS_SONAR
	 #if defined (USE_LIDAR)
   	Usart4_Init(115200L); 
	 #else
	 	Usart4_Init(9600);
	#endif
	#endif
	
	#if EN_DMA_UART4 
	MYDMA_Config(DMA1_Stream4,DMA_Channel_4,(u32)&UART4->DR,(u32)SendBuff4,SEND_BUF_SIZE4+2,0);//DMA2,STEAM7,CH4,外设为串口1,存储器为SendBuff,长度为:SEND_BUF_SIZE.
	#endif
	#if defined(SONAR_USE_UART)  
		#if defined(URM07)
		Usart3_Init(19200); 
		#else
		Usart3_Init(9600L);    	
		#endif
		#if defined(USE_LIDAR)
		  Usart3_Init(115200);
		#endif
	#else
	Ultrasonic_Init();
	#endif
	#if EN_DMA_UART3
	MYDMA_Config(DMA1_Stream3,DMA_Channel_4,(u32)&USART3->DR,(u32)SendBuff3,SEND_BUF_SIZE3+2,2);
	#endif

	#if FLOW_USE_IIC
	Soft_I2C_Init_PX4();      //FLOW PX4 IIC
	#else
  Uart5_Init(576000);			//FLOW PX4
	#endif
	#if FLOW_USE_OPENMV
  Uart5_Init(576000L);			//FLOW PX4
  #endif
	#if USE_ANO_FLOW
	Uart5_Init(500000L);			
	#endif
	#if USE_UWB_AS_POS
		Usart4_Init(460800);
	#endif
	#if USE_GPS_U4
		Drv_GpsPin_Init();
	#endif

//-----------------------Mode &  Flag init--------------------	
//--system
	fly_ready=0;
	mode.en_imu_ekf=0;
	three_wheel_car.gain[0]=1.68;
	three_wheel_car.car_mode=1;//0 遥控   2 前进 1 往返 3 圆
	//-----------------DMA Init--------------------------
#if EN_DMA_UART4 
	USART_DMACmd(UART4,USART_DMAReq_Tx,ENABLE);    
	MYDMA_Enable(DMA1_Stream4,SEND_BUF_SIZE4+2);     
#endif
#if EN_DMA_UART2
	USART_DMACmd(USART2,USART_DMAReq_Tx,ENABLE); 
	MYDMA_Enable(DMA1_Stream6,SEND_BUF_SIZE2+2);    
#endif
#if EN_DMA_UART3
	USART_DMACmd(USART3,USART_DMAReq_Tx,ENABLE);   
	MYDMA_Enable(DMA1_Stream3,SEND_BUF_SIZE3+2);    
#endif
#if EN_DMA_UART1 
	USART_DMACmd(USART1,USART_DMAReq_Tx,ENABLE);   
	MYDMA_Enable(DMA2_Stream7,SEND_BUF_SIZE1+2);    
#endif	

  TIM3_Int_Init(50-1,8400-1);	
	Delay_ms(20);
	Outer_Compass_init();//外置罗盘初始化
	IWDG_Init(4,500*3); //与分频数为64,重载值为500,溢出时间为1s	
	OSInit();  	 				
	OSTaskCreate(start_task,(void *)0,(OS_STK *)&START_TASK_STK[START_STK_SIZE-1],START_TASK_PRIO );//创建起始任务
	OSStart();	    
}
 

//开始任务
void start_task(void *pdata)
{
  OS_CPU_SR cpu_sr=0;
	u8 err;	    	    
	pdata = pdata; 	
	msg_key=OSMboxCreate((void*)0);		//创建消息邮箱
	q_msg=OSQCreate(&MsgGrp[0],256);	//创建消息队列
 	flags_key=OSFlagCreate(0,&err); 	//创建信号量集		  
	  
	OSStatInit();					//初始化统计任务.这里会延时1秒钟左右
	//注册软件定时器
	tmr1=OSTmrCreate(10,10,OS_TMR_OPT_PERIODIC,(OS_TMR_CALLBACK)tmr1_callback,0,"tmr1",&err);		//100ms执行一次  cpu使用率
	OSTmrStart(tmr1,&err);//启动软件定时器1				 	
	tmr2=OSTmrCreate(10,5,OS_TMR_OPT_PERIODIC,(OS_TMR_CALLBACK)tmr2_callback,0,"tmr2",&err);		//50ms执行一次  LED&&MODE
	OSTmrStart(tmr2,&err);//启动软件定时器1				 	
 	OS_ENTER_CRITICAL();			//进入临界区(无法被中断打断)    
 	//注册线程 	
	#if !USE_UKF_FROM_AUTOQUAD	
	OSTaskCreate(outer_task,(void *)0,(OS_STK*)&OUTER_TASK_STK[OUTER_STK_SIZE-1],OUTER_TASK_PRIO);
	#endif
	#if !EN_TIM_INNER
	OSTaskCreate(inner_task,(void *)0,(OS_STK*)&INNER_TASK_STK[INNER_STK_SIZE-1],INNER_TASK_PRIO);
	#endif
	#if !UKF_IN_ONE_THREAD
	OSTaskCreate(ekf_task,(void *)0,(OS_STK*)&EKF_TASK_STK[EKF_STK_SIZE-1],EKF_TASK_PRIO);
	#endif
	OSTaskCreate(flow_task1,(void *)0,(OS_STK*)&FLOW_TASK_STK[FLOW_STK_SIZE-1],FLOW_TASK_PRIO);
	#if !UKF_IN_ONE_THREAD
	OSTaskCreate(baro_task,(void *)0,(OS_STK*)&BARO_TASK_STK[BARO_STK_SIZE-1],BARO_TASK_PRIO);
	#endif
	OSTaskCreate(sonar_task,(void *)0,(OS_STK*)&SONAR_TASK_STK[SONAR_STK_SIZE-1],SONAR_TASK_PRIO);	
	OSTaskCreate(error_task,(void *)0,(OS_STK*)&ERROR_TASK_STK[ERROR_STK_SIZE-1],ERROR_TASK_PRIO);
	//--
 	OSTaskSuspend(START_TASK_PRIO);	//挂起起始任务.
	OS_EXIT_CRITICAL();				//退出临界区(可以被中断打断)
}
   

//信号量集处理任务
void flags_task(void *pdata)
{	
	u16 flags;	
	u8 err;	    						 
	while(1)
	{
		flags=OSFlagPend(flags_key,0X001F,OS_FLAG_WAIT_SET_ANY,0,&err);//等待信号量 		
		OSFlagPost(flags_key,0X001F,OS_FLAG_CLR,&err);//全部信号量清零
 	}
}
   		    

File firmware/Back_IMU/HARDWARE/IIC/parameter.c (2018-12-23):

#include "include.h"
#include "mpu6050.h"
#include "hml5833l.h"
#include "att.h"
#include "string.h"
#include "height_ctrl.h"
#include "eso.h"
#define SENSOR_SETUP_FILE      "sensor.bin"
#define PID_SETUP_FILE         "pid.bin"
u8 flash_init_error;
static sensor_setup_t sensor_setup;
static pid_setup_t pid_setup;


static void  Param_SetSettingToFC(void) //fly thr 45% at 4s full 4.4Ah
{
	memcpy(&mpu6050.Acc_Offset,&sensor_setup.Offset.Accel,sizeof(xyz_f_t));
	memcpy(&mpu6050.Gyro_Offset,&sensor_setup.Offset.Gyro,sizeof(xyz_f_t));
	memcpy(&ak8975.Mag_Offset,&sensor_setup.Offset.Mag,sizeof(xyz_f_t));
	mpu6050.Temprea_Offset = sensor_setup.Offset.Temperature;
#if defined(ZHOU_550)//-----------------------------------------550----------------------------------	
//--------------------------------------Angle-------------------------------
	//p
  pid_setup.groups.ctrl2.roll.kp=pid_setup.groups.ctrl2.pitch.kp =0.45;//0.35;//28;//0.425;//0.425;//<-----------mini0.45 for 4050  0.4 for 6030 WT
	SPID.IP=pid_setup.groups.ctrl2.roll.kp*1000;
	//i
	pid_setup.groups.ctrl2.roll.ki =pid_setup.groups.ctrl2.pitch.ki = 0.15;//0.25;//0.05;
	SPID.II=pid_setup.groups.ctrl2.roll.ki*1000;
	//d
	pid_setup.groups.ctrl2.roll.kd  = pid_setup.groups.ctrl2.pitch.kd =0.35;//0.3;//2;//0.425;//35;//<-------------mini
	SPID.ID=pid_setup.groups.ctrl2.roll.kd*1000;
	//---------------------------------------GRO-----------------------------
	//p
	pid_setup.groups.ctrl1.roll.kp=pid_setup.groups.ctrl1.pitch.kp = 0.45;//0.3;//0.425;//0.35;//<-----------mini  WT
	SPID.OP=pid_setup.groups.ctrl1.roll.kp*1000;
	//i
  pid_setup.groups.ctrl1.roll.ki =pid_setup.groups.ctrl1.pitch.ki =0.1;// 0.05;//0.1;
	SPID.OI=pid_setup.groups.ctrl1.roll.ki*1000;
	//d
	pid_setup.groups.ctrl1.roll.kd=pid_setup.groups.ctrl1.pitch.kd = 4;//4;//2.0;
	SPID.OD=pid_setup.groups.ctrl1.roll.kd*1000;
	//----------------------------------YAW---------------------------------
	pid_setup.groups.ctrl2.yaw.kp   = 0.8;//0.4;//0.8;	
	SPID.YD=pid_setup.groups.ctrl2.yaw.kp*1000;
	pid_setup.groups.ctrl2.yaw.ki   = 0.05;	
	SPID.YI=pid_setup.groups.ctrl2.yaw.ki*1000;
  pid_setup.groups.ctrl2.yaw.kd   = 0.3;//0.1;//0.3;
	//------------------------------------
	pid_setup.groups.ctrl1.yaw.kp   = 0.8;//1.2;//0.8;
	SPID.YP=pid_setup.groups.ctrl1.yaw.kp*1000;	
	
	pid_setup.groups.ctrl1.yaw.ki   = 0.1;//1.0;//0.5;//0.1;	
	pid_setup.groups.ctrl1.yaw.kd   = 1.0;//1.0;//1.5;	
	pid_setup.groups.ctrl1.roll.kdamp=pid_setup.groups.ctrl1.pitch.kdamp = 1;
	pid_setup.groups.ctrl1.yaw.kdamp   = 1;
	//--------------------------------------------光流定位---------------------------
		pid.nav.out.p=1;////0.35;
		pid.nav.out.i=0;//8;//(wt)
		pid.nav.in.p =0.7;//1.25;//3.5;//0.365;//0.350;//0.4;//fix 2015.10.21 导航均值滤波 阴天//0.025;//150
		pid.nav.in.i =0.00;
		pid.nav.in.d =0.0;//0.250;
		pid.nav.out.dead= 0.02;//位置死区mm
		pid.nav.in.dead=  0.02;//3;//速度死区mm/s
		pid.nav.in.dead2=  0.02;//pid.nav.in.dead*1.5;//4.5;//速度积分死区mm/s
//-----------------------------壁障----------------------------------
	pid.avoid.out.p=0.1;
//----------------------------ESO------------------------------------
	eso_att_outter[PITr].n=eso_att_outter[ROLr].n=eso_att_outter[YAWr].n=15;
  eso_att_inner[PITr].n=eso_att_inner[ROLr].n=eso_att_inner[YAWr].n=66;
	
	
#elif defined(ZHOU_350)//----------------------------------------------350-------------------------------------------------------------
//--------------------------------------Angle------------------------------------	
	//p
  pid_setup.groups.ctrl2.roll.kp=pid_setup.groups.ctrl2.pitch.kp =0.35;//0.35;//28;//0.425;//0.425;//<-----------mini0.45 for 4050  0.4 for 6030 WT
	SPID.IP=pid_setup.groups.ctrl2.roll.kp*1000;
	//i
	pid_setup.groups.ctrl2.roll.ki =pid_setup.groups.ctrl2.pitch.ki = 0.15;//0.25;//0.05;
	SPID.II=pid_setup.groups.ctrl2.roll.ki*1000;
	//d
	pid_setup.groups.ctrl2.roll.kd  = pid_setup.groups.ctrl2.pitch.kd =0.3;//0.3;//2;//0.425;//35;//<-------------mini
	SPID.ID=pid_setup.groups.ctrl2.roll.kd*1000;
	//---------------------------------------GRO-----------------------------------
	//p
	pid_setup.groups.ctrl1.roll.kp=pid_setup.groups.ctrl1.pitch.kp = 0.3;//0.3;//0.425;//0.35;//<-----------mini  WT
	SPID.OP=pid_setup.groups.ctrl1.roll.kp*1000;
	//i
  pid_setup.groups.ctrl1.roll.ki =pid_setup.groups.ctrl1.pitch.ki =0.1;// 0.05;//0.1;
	SPID.OI=pid_setup.groups.ctrl1.roll.ki*1000;
	//d
	pid_setup.groups.ctrl1.roll.kd=pid_setup.groups.ctrl1.pitch.kd = 4;//4;//2.0;
	SPID.OD=pid_setup.groups.ctrl1.roll.kd*1000;
	//------------------------------------YAW--------------------------------------
	pid_setup.groups.ctrl2.yaw.kp   = 0.8;//0.4;//0.8;	
	SPID.YD=pid_setup.groups.ctrl2.yaw.kp*1000;
	pid_setup.groups.ctrl2.yaw.ki   = 0.05;	
	SPID.YI=pid_setup.groups.ctrl2.yaw.ki*1000;
  pid_setup.groups.ctrl2.yaw.kd   = 0.3;//0.1;//0.3;
	//------------------------------------
	pid_setup.groups.ctrl1.yaw.kp   = 0.8;//1.2;//0.8;
	SPID.YP=pid_setup.groups.ctrl1.yaw.kp*1000;
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

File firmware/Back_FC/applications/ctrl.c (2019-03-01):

#include "flash.h"
#include "ctrl.h"
#include "height_ctrl.h"
#include "fly_mode.h"
#include "quar.h"
#include "eso.h"
ctrl_t ctrl_1;
ctrl_t ctrl_2;
FAN fan;
void Ctrl_Para_Init()		//设置默认参数
{
//====================================
	ctrl_1.PID[PIDROLL].kdamp  = 1;
	ctrl_1.PID[PIDPITCH].kdamp = 1;
	ctrl_1.PID[PIDYAW].kdamp 	 = 1;
	
	ctrl_1.FB = 0.20;   //外  0<fb<1
}

xyz_f_t except_A = {0,0,0};

xyz_f_t ctrl_angle_offset = {0,0,0};

xyz_f_t compensation;

void CTRL_2(float T)
{static u16 init_yaw;
 int RC_DEAD=30;
	if(mode_oldx.flow_hold_position==0)
		RC_DEAD=0;
//=========================== 期望角度 ========================================
	#if defined(INDOOR_FPV_SERCH)
	except_A.x  = -MAX_CTRL_ANGLE  *( my_deathzoom( ( CH_filter[ROL]) ,0,RC_DEAD )/500.0f );   //30
	except_A.y  = -MAX_CTRL_ANGLE  *( my_deathzoom( ( CH_filter[PIT]) ,0,RC_DEAD )/500.0f );  //30
	#else
	#if USE_RC_INVERT
	except_A.x  = -MAX_CTRL_ANGLE  *( my_deathzoom( ( CH_filter[ROL]) ,0,RC_DEAD )/500.0f );   //30
	except_A.y  = -MAX_CTRL_ANGLE  *( my_deathzoom( ( CH_filter[PIT]) ,0,RC_DEAD )/500.0f );  //30
	#else
	except_A.x  = MAX_CTRL_ANGLE  *( my_deathzoom( ( CH_filter[ROL]) ,0,RC_DEAD )/500.0f );   //30
	except_A.y  = MAX_CTRL_ANGLE  *( my_deathzoom( ( CH_filter[PIT]) ,0,RC_DEAD )/500.0f );  //30
	#endif
	#endif
	if( !Thr_Low )
	{
    if(smart.rc.ATT_MODE==SMART_MODE_POS&&smart.att.z!=0)
			except_A.z =  smart.att.z ;
		#if PX4_SDK
		else if(px4.connect&&my_deathzoom_2( (CH_filter[YAW]) ,0,20 )!=0)
		except_A.z=Yaw_fc;  
		#endif
		else
		except_A.z += (s16)( MAX_CTRL_YAW_SPEED_RC *( my_deathzoom_2( (CH_filter[YAW]) ,0,20 )/500.0f ) ) *T ;  //50
	}
	else
	{
		#if EN_ATT_CAL_FC
		except_A.z += 1 *3.14 *T *( Yaw_fc - except_A.z );
		#else
		except_A.z += 1 *3.14 *T *( Yaw - except_A.z );
		#endif
	}
	if(init_yaw++>500){init_yaw=502;
	except_A.z = To_180_degrees(except_A.z);
	}else
	except_A.z = Yaw_fc;
	if(mode_oldx.flow_hold_position>0&&except_A.y==0&&except_A.x==0)
	{
			if((module.gps||module.flow||module.pi||module.pi_flow)==1){
				except_A.y=LIMIT(nav[PITr],-MAX_CTRL_ANGLE,MAX_CTRL_ANGLE);
				except_A.x=LIMIT(nav[ROLr],-MAX_CTRL_ANGLE,MAX_CTRL_ANGLE);
			}
	}
  if(smart.rc.ATT_MODE==SMART_MODE_SPD&&smart.att_rate.z!=0)
	{except_A.z  +=  smart.att_rate.z*T; except_A.z = To_180_degrees(except_A.z);}
	static u8 yaw_trig;
	if(mode_oldx.att_pid_tune)
	{
	{	
	if(KEY_SEL[0])//TRIG for tuning
	#if !TUNING_Z	
		#if TUNING_X	
		except_A.x=-15;
		#else
		except_A.y=15;
		#endif
	#else
	{if(yaw_trig==0){except_A.z=Yaw_fc+15;yaw_trig=1;}}
	#endif
	else
	#if !TUNING_Z		
		#if TUNING_X	
		except_A.x=LIMIT(except_A.x,-15,15);	
		#else
		except_A.y=LIMIT(except_A.y,-15,15);	
		#endif
	#else
	 { except_A.x=except_A.y=yaw_trig=0;}
	#endif
  }

  if(mode_oldx.use_px4_err){
	cal_ero_outter_so3(); 
  ctrl_2.err.x =  my_deathzoom_21(ero_angle_px4[0],0.0);
	ctrl_2.err.y =  my_deathzoom_21(ero_angle_px4[1],0.0);
	#if EN_ATT_CAL_FC
	ctrl_2.err.z =  my_deathzoom_21(LIMIT(To_180_degrees( ctrl_angle_offset.z + except_A.z - Yaw_fc	 ),-YAW_ERO_MAX,YAW_ERO_MAX),0.5);//*LIMIT(ero_angle_px4[3],0.5,1);
	#else	
	ctrl_2.err.z =  my_deathzoom_21(LIMIT(To_180_degrees( ctrl_angle_offset.z + except_A.z - Yaw	 ),-YAW_ERO_MAX,YAW_ERO_MAX),0.5);//*LIMIT(ero_angle_px4[3],0.5,1);
	#endif
	}else{	
	ctrl_2.err.x =  my_deathzoom_21(To_180_degrees( ctrl_angle_offset.x + except_A.x - Rol_fc  ),0.1);
	ctrl_2.err.y =  my_deathzoom_21(To_180_degrees( ctrl_angle_offset.y + except_A.y - Pit_fc ),0.1);}
	#if EN_ATT_CAL_FC
	ctrl_2.err.z =  my_deathzoom_21(LIMIT(To_180_degrees( ctrl_angle_offset.z + except_A.z - Yaw_fc	 ),-YAW_ERO_MAX,YAW_ERO_MAX),0.5);//*LIMIT(ero_angle_px4[3],0.5,1);
	#else	
	ctrl_2.err.z =  my_deathzoom_21(LIMIT(To_180_degrees( ctrl_angle_offset.z + except_A.z - Yaw	 ),-YAW_ERO_MAX,YAW_ERO_MAX),0.5);//*LIMIT(ero_angle_px4[3],0.5,1);
	#endif	
	}//normal 
	else{	//使用SO3下误差计算
	
	cal_ero_outter_so3(); 
  /* 得到角度误差 */
	if(mode_oldx.use_px4_err){
  ctrl_2.err.x =  my_deathzoom_21(ero_angle_px4[0],0.0);
	ctrl_2.err.y =  my_deathzoom_21(ero_angle_px4[1],0.0);
	#if EN_ATT_CAL_FC
	ctrl_2.err.z =  my_deathzoom_21(LIMIT(To_180_degrees( ctrl_angle_offset.z + except_A.z - Yaw_fc	 ),-YAW_ERO_MAX,YAW_ERO_MAX),0.5);//*LIMIT(ero_angle_px4[3],0.5,1);
	#else	
	ctrl_2.err.z =  my_deathzoom1(LIMIT(To_180_degrees( ctrl_angle_offset.z + except_A.z - Yaw	 ),-YAW_ERO_MAX,YAW_ERO_MAX),0.5);//*LIMIT(ero_angle_px4[3],0.5,1);
	#endif
	}else{	
	ctrl_2.err.x =  my_deathzoom_21(To_180_degrees( ctrl_angle_offset.x + except_A.x - Rol_fc  ),0.1);
	ctrl_2.err.y =  my_deathzoom_21(To_180_degrees( ctrl_angle_offset.y - except_A.y - Pit_fc ),0.1);}
	#if EN_ATT_CAL_FC
	ctrl_2.err.z =  my_deathzoom_21(LIMIT(To_180_degrees( ctrl_angle_offset.z + except_A.z - Yaw_fc	 ),-YAW_ERO_MAX,YAW_ERO_MAX),0.5);//*LIMIT(ero_angle_px4[3],0.5,1);
	#else	
	ctrl_2.err.z =  my_deathzoom_21(LIMIT(To_180_degrees( ctrl_angle_offset.z + except_A.z - Yaw	 ),-YAW_ERO_MAX,YAW_ERO_MAX),0.5);//*LIMIT(ero_angle_px4[3],0.5,1);
	#endif
	}

	/* 计算角度误差权重 */
	ctrl_2.err_weight.x = ABS(ctrl_2.err.x)/ANGLE_TO_MAX_AS;
	ctrl_2.err_weight.y = ABS(ctrl_2.err.y)/ANGLE_TO_MAX_AS;
	ctrl_2.err_weight.z = ABS(ctrl_2.err.z)/ANGLE_TO_MAX_AS;
//	/* 角度误差微分（跟随误差曲线变化）*/
	ctrl_2.err_d.x = 10 *ctrl_2.PID[PIDROLL].kd  *(ctrl_2.err.x - ctrl_2.err_old.x) *( 0.005f/T ) ;
	ctrl_2.err_d.y = 10 *ctrl_2.PID[PIDPITCH].kd *(ctrl_2.err.y - ctrl_2.err_old.y) *( 0.005f/T ) ;
	ctrl_2.err_d.z = 10 *ctrl_2.PID[PIDYAW].kd 	 *(ctrl_2.err.z - ctrl_2.err_old.z) *( 0.005f/T ) ;
//	/* 角度误差积分 */
//	ctrl_2.err_i.x += ctrl_2.PID[PIDROLL].ki  *ctrl_2.err.x *T;
//	ctrl_2.err_i.y += ctrl_2.PID[PIDPITCH].ki *ctrl_2.err.y *T;
 	ctrl_2.err_i.z += ctrl_2.PID[PIDYAW].ki 	*ctrl_2.err.z *T;
//	/* 角度误差积分分离 */
//	ctrl_2.eliminate_I.x = Thr_Weight *CTRL_2_INT_LIMIT;
//	ctrl_2.eliminate_I.y = Thr_Weight *CTRL_2_INT_LIMIT;
	ctrl_2.eliminate_I.z = Thr_Weight *CTRL_2_INT_LIMIT;
//	/* 角度误差积分限幅 */
//	ctrl_2.err_i.x = LIMIT( ctrl_2.err_i.x, -ctrl_2.eliminate_I.x,ctrl_2.eliminate_I.x );
//	ctrl_2.err_i.y = LIMIT( ctrl_2.err_i.y, -ctrl_2.eliminate_I.y,ctrl_2.eliminate_I.y );
	ctrl_2.err_i.z = LIMIT( ctrl_2.err_i.z, -ctrl_2.eliminate_I.z,ctrl_2.eliminate_I.z );
//	/* 记录历史数据 */	
	ctrl_2.err_old.x = ctrl_2.err.x;
	ctrl_2.err_old.y = ctrl_2.err.y;
	ctrl_2.err_old.z = ctrl_2.err.z;	
	
	/* 对用于计算比例项输出的角度误差限幅 */
	ctrl_2.err.x = LIMIT( ctrl_2.err.x, -90, 90 );
	ctrl_2.err.y = LIMIT( ctrl_2.err.y, -90, 90 );
	if(ctrl_1.zrate_limit!=0)
	 ctrl_2.err.z = LIMIT( ctrl_2.err.z, -ctrl_1.zrate_limit,ctrl_1.zrate_limit );
	else
	 ctrl_2.err.z = LIMIT( ctrl_2.err.z, -90, 90 );
	/* 角度PID输出 */
	ctrl_2.out.x = ctrl_2.PID[PIDROLL].kp  *( ctrl_2.err.x + ctrl_2.err_d.x + ctrl_2.err_i.x );	//rol
	ctrl_2.out.y = ctrl_2.PID[PIDPITCH].kp *( ctrl_2.err.y + ctrl_2.err_d.y + ctrl_2.err_i.y );  //pit
	
//	if(smart.rc.ATT_MODE==SMART_MODE_SPD)
//		ctrl_2.out.z =  smart.att_rate.z ;  
//	else 
		ctrl_2.out.z = ctrl_2.PID[PIDYAW].kp   *( ctrl_2.err.z + ctrl_2.err_d.z + ctrl_2.err_i.z );
}
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

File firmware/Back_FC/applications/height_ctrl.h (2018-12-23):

#ifndef __HEIGHT_CTRL_H
#define __HEIGHT_CTRL_H

#include "stm32f4xx.h"

#include "parameter.h"

#define _xyz_f_t xyz_f_t

#define THR_TAKE_OFF_LIMIT 450
typedef struct
{
	float m_acc;
	float m_speed;
	float m_height;
	float fusion_acc;
	float fusion_speed;
	float fusion_height;

}_hc_value_st;
extern float ultra_ctrl_out_use,ultra_dis_lpf;
extern _hc_value_st hc_value;
extern u8 height_ctrl_mode;
float auto_take_off_land(float dT,u8 ready);
float Height_Ctrl(float T,float thr,u8 ready,float en);
void h_pid_init(void);
extern int exp_height;
extern float ALT_VEL_SONAR,ALT_POS_SONAR,ALT_POS_SONAR2,ALT_VEL_BMP,ALT_POS_BMP,ALT_VEL_BMP_EKF,ALT_POS_BMP_EKF;
extern int baroAlt,ultra_distance;
typedef struct
{ float exp;
	float err;
	float err_old;
	float err_d;
	float err_i;
	float pid_out;
	float err_weight;
	float now;
  u8 hold_alt_flag;
}_st_height_pid_v;

typedef struct
{
	float kp;
	float kd;
	float ki;
  float fp;
	float ero_r[3];
}_st_height_pid;

void Height_Ctrl1(float T,float thr);

void Ultra_PID_Init(void);

void WZ_Speed_PID_Init(void);

void height_speed_ctrl1(float T,float thr,float exp_z_speed,float );

void Baro_Ctrl1(float T,float thr);

void Ultra_Ctrl1(float T,float thr);
void Ultra_Ctrl2(float T,float thr);
extern float ultra_ctrl_out;

extern float height_ctrl_out;

extern u8 baro_ctrl_start;

extern float ultra_speed,wz_speed,baro_height;
#define ULTRA_SPEED 		 300    // mm/s
#define ULTRA_MAX_HEIGHT 1500   // mm
#define ULTRA_INT        300    // 积分幅度

#define H_INNER 10
#define F_POS_SPD 20
#define F_POS 2
#define H_OUTTER 2*H_INNER
#define MAX_VERTICAL_SPEED 1500.0
extern _st_height_pid_v wz_speed_pid_v;
extern _st_height_pid wz_speed_pid;
extern _st_height_pid_v ultra_ctrl;
extern _st_height_pid ultra_pid;
extern _st_height_pid track_pid[10];
int height_test(float T);
#endif

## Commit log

2019-01-26 更新API和SDK
2019-01-27 更新机型
2019-01-29 更新原理图
2019-03-14 update material
    [OLDX多旋翼飞行器解决方案整机物料.xls]
